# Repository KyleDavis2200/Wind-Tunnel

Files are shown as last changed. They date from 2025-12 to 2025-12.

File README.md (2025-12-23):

# Wind Tunnel
A DIY small scale wind tunnel made from everyday materials.


# Features
* Made from basic materials, allowing it to be remade by other people.
* Sturdy construction prevents collapse under high wind flow.
* Humidifier visualizes airflow to be seen through the viewing window.
* Includes jigs and drawings to aid in construction.

# Pictures







# Background

This wind tunnel uses a humidifier to create steam that will show the airflow over the model. The model is inserted into the tunnel, the window is screwed on, and then air flows through a funnel and a hose attached to the humidifier, into a straw inserted into the top of the model. The fan has a low, medium, and high speed setting allowing airflow to be visualized at different speeds. Most of the wind tunnel is built out of OSB, a cheap type of wood that is easily accessible. The collector part can be 3D printed, as that is the easiest way to make the smooth curve needed to guide the air into the tunnel. This wind tunnel is a little under 4 feet long and 9" square, and it can be built for under $100 if you already have a humidifier on hand.

# Bill of Materials

|Item |Price|Quantity |Total Price|Link |Notes: |
|---|-----|---|---|---|---|
|Fan |41.3 |1 |41.3 |https://www.amazon.com/dp/B0F11G5SWD?ref=ppx_yo2ov_dt_b_fed_asin_title&th=1 |*Sourcing from Amazon because a comparable fan on Aliexpress is usually more expensive, does not have adjustable speed, and may not have the right plug. We are also on a time crunch so I have already purchased this.|
|4'x8' 1/2" Sheet  of OSB |14.29|1 |14.29 |https://www.lowes.com/pd/1-2-CAT-PS2-10-OSB-Sheathing-Application-as-4-x-8/1000068915 | |
|1/4" ID, 3/8" OD Clear Tubing 10'|3.58 |1 |3.58 |https://www.lowes.com/pd/EZ-FLO-1-4-in-Inner-Diameter-x-10-ft-PVC-Clear-Vinyl-Tubing/1000365025 |*Sourcing from Lowe's because we have already bought this from there and are planning to get reimbursed |
|8"x10"x0.08" Acrylic |4.78 |1 |4.78 |https://www.lowes.com/pd/OPTIX-0-08-in-T-x-8-in-W-x-10-in-L-Clear-Acrylic-Sheet/3143395 |*Sourcing from Lowe's because we have already bought this from there and are planning to get reimbursed |
|#8 Wood Screws 1 5/8" Long |6.98 |1 (box of 75)|6.98 |https://www.lowes.com/pd/Hillman-8-x-1-5-8-in-Ceramic-Deck-Screws-75-Count/999995034 | |
|Caulk |2.98 |1 |2.98 |https://www.lowes.com/pd/DAP-Alex-Plus-10-1-oz-Clear-Paintable-Latex-Caulk/5004004945 |*Using to seal gaps that are letting air flow out through the corners of the tunnel. |
|Black Spray Paint |7.48 |1 |7.48 |https://www.lowes.com/pd/Krylon-FUSION-ALL-IN-ONE-Matte-Black-Spray-Paint-and-Primer-In-One-NET-WT-12-oz/1000460293|*Sourcing from Lowe's because we have already bought this from there and are planning to get reimbursed. Using to paint the inside of the tunnel black to provide contrast for the steam. |
|Humidifier |N/A  |1 |N/A |N/A |*Already have |
|Plastic Straw |N/A  |1 |N/A |N/A |*Already have |
|PLA Filament |N/A  |1kg |N/A |N/A |*Already have |
| | | | | | |
|Total Price: |N/A  |N/A |81.39 |N/A | |

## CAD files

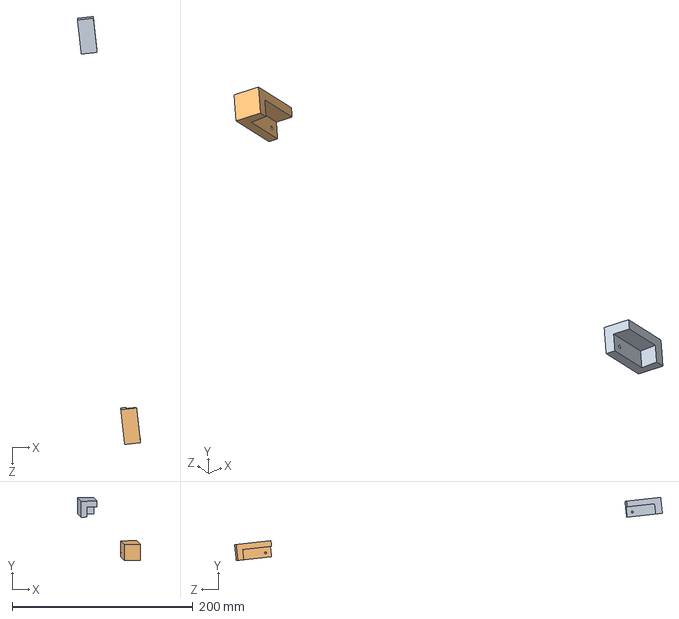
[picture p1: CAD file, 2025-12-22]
CAD/Jigs/Jigs HI.STEP
69.9 x 70.1 x 473.6 mm

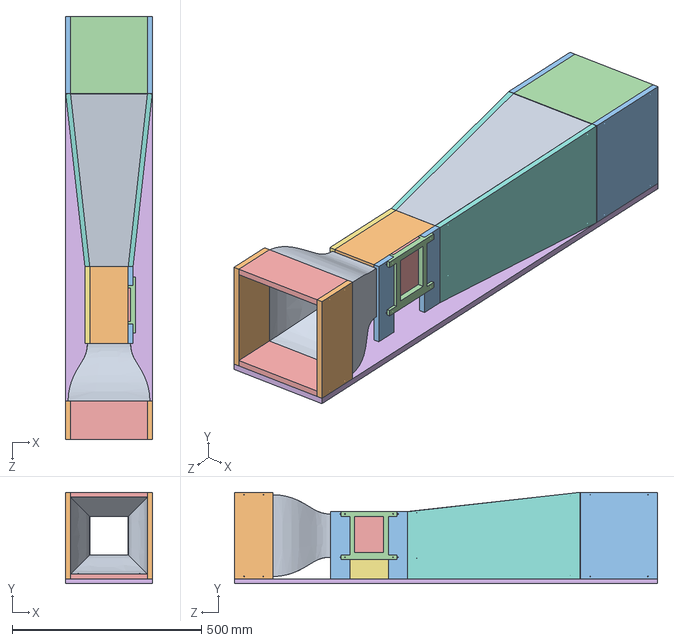
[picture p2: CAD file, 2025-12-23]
CAD/Wind Tunnel.STEP
228.6 x 241.4 x 1117.6 mm

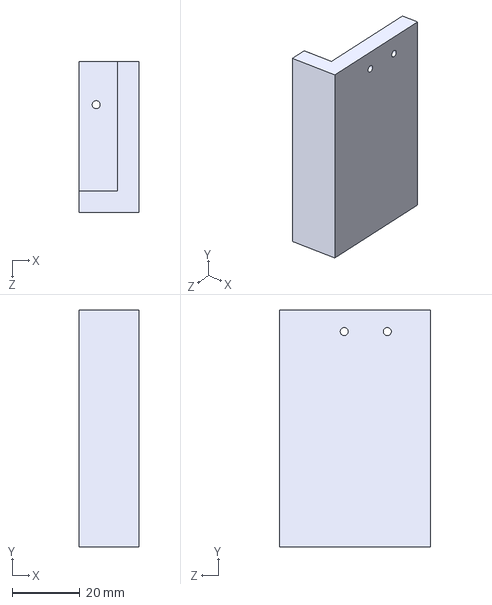
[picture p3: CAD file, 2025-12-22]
CAD/Jigs/Jig C.STEP
17.8 x 69.9 x 44.4 mm

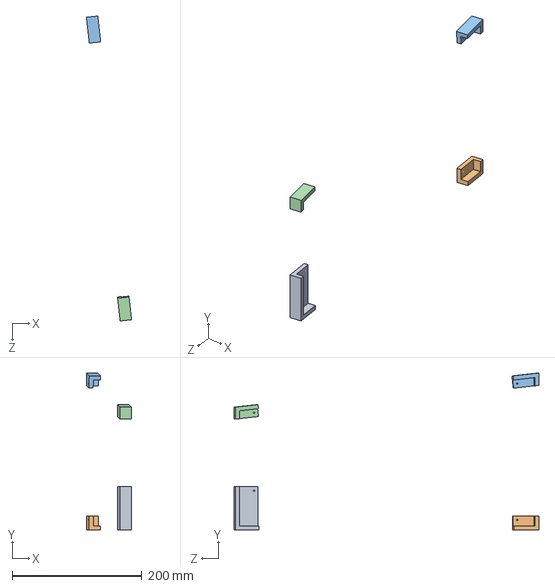
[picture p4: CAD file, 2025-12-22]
CAD/Jigs/Jigs DEFG.STEP
69.7 x 242.1 x 470.4 mm

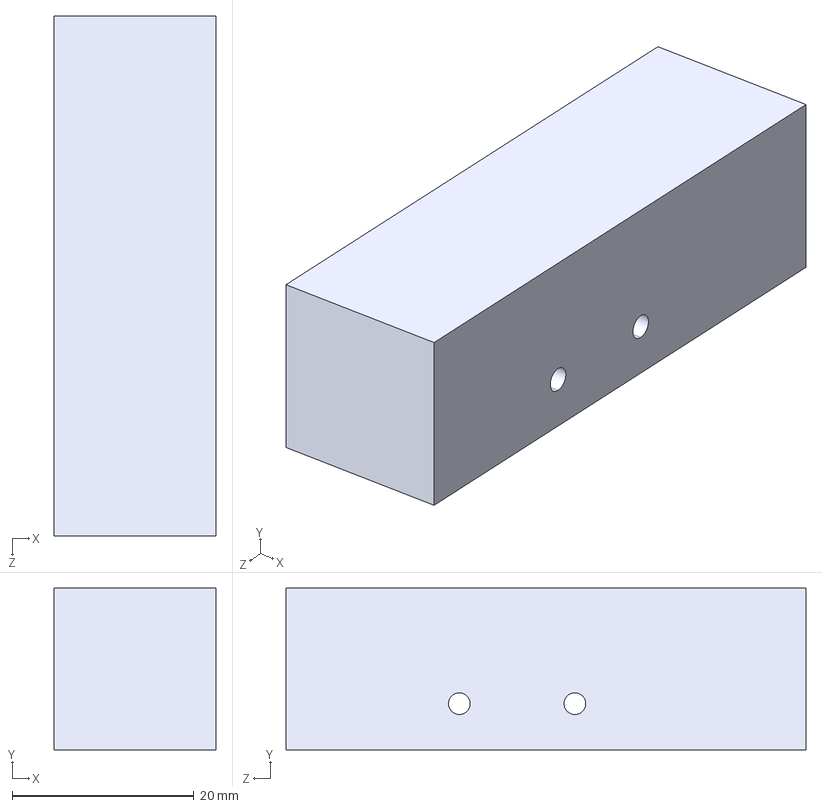
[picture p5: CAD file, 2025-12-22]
CAD/Jigs/Jig B.STEP
17.8 x 17.8 x 57.2 mm

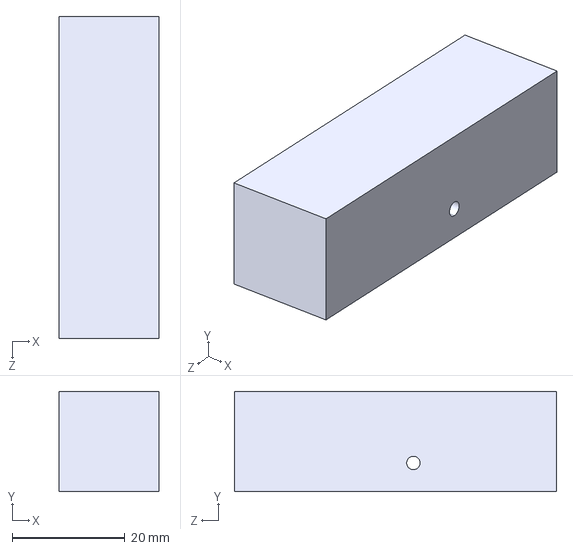
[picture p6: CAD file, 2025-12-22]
CAD/Jigs/Jig A.STEP
17.8 x 17.8 x 57.2 mm

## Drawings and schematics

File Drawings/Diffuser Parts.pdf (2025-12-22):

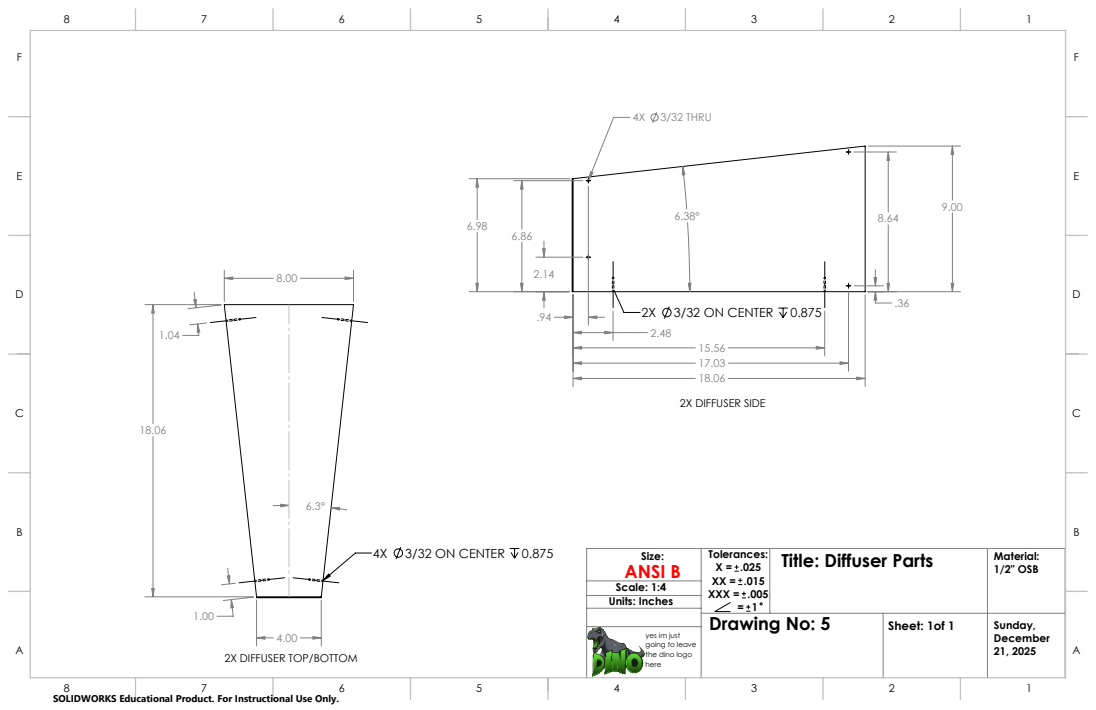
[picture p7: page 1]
Drawing No: 5; ANSI B; XXX =; Title: Diffuser Parts; Material:; 1/2" OSB; Scale: 1:4 Units: Inches; Sheet: 1of 1; 4X 3/32 THRU; 2X 3/32 ON CENTER 0.875; 4X 3/32 ON CENTER 0.875; 2X DIFFUSER SIDE; 2X DIFFUSER TOP/BOTTOM A

yes im just
going to leave
the dino logo
here

SOLIDWORKS Educational Product. For Instructional Use Only.

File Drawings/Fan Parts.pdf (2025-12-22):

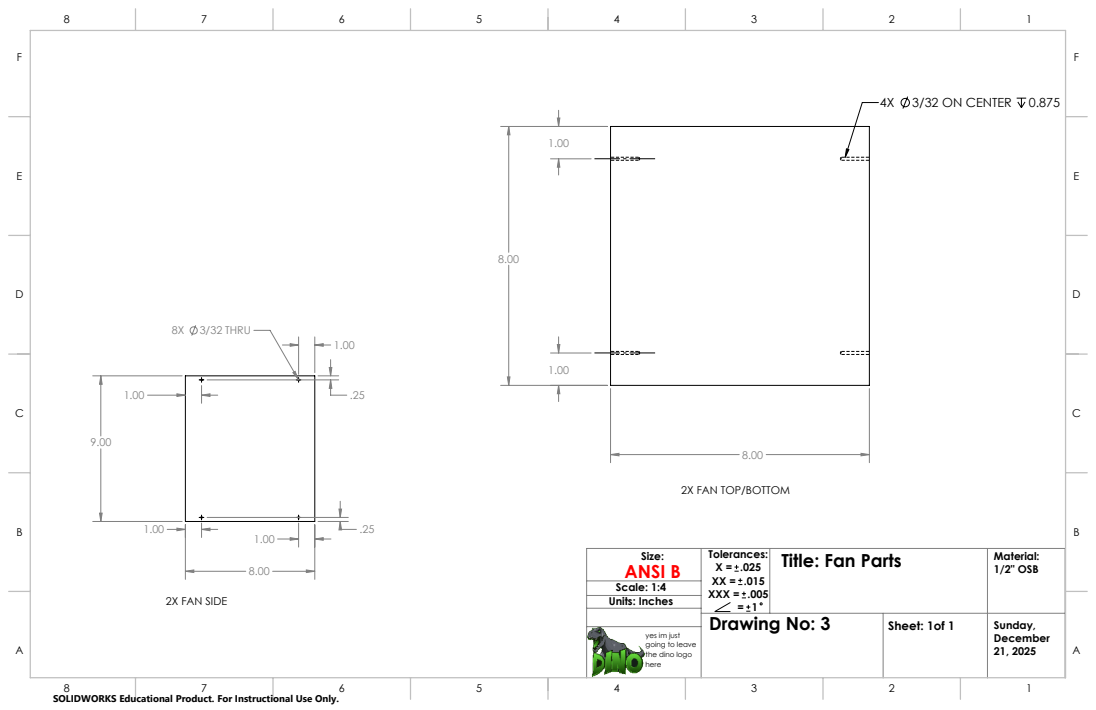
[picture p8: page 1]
Drawing No: 3; ANSI B; XXX =; Title: Fan Parts; Material:; 1/2" OSB; Scale: 1:4 Units: Inches; Sheet: 1of 1; 8X 3/32 THRU; 4X 3/32 ON CENTER 0.875; 2X FAN SIDE

2X FAN TOP/BOTTOM

yes im just
going to leave
the dino logo
here

SOLIDWORKS Educational Product. For Instructional Use Only.

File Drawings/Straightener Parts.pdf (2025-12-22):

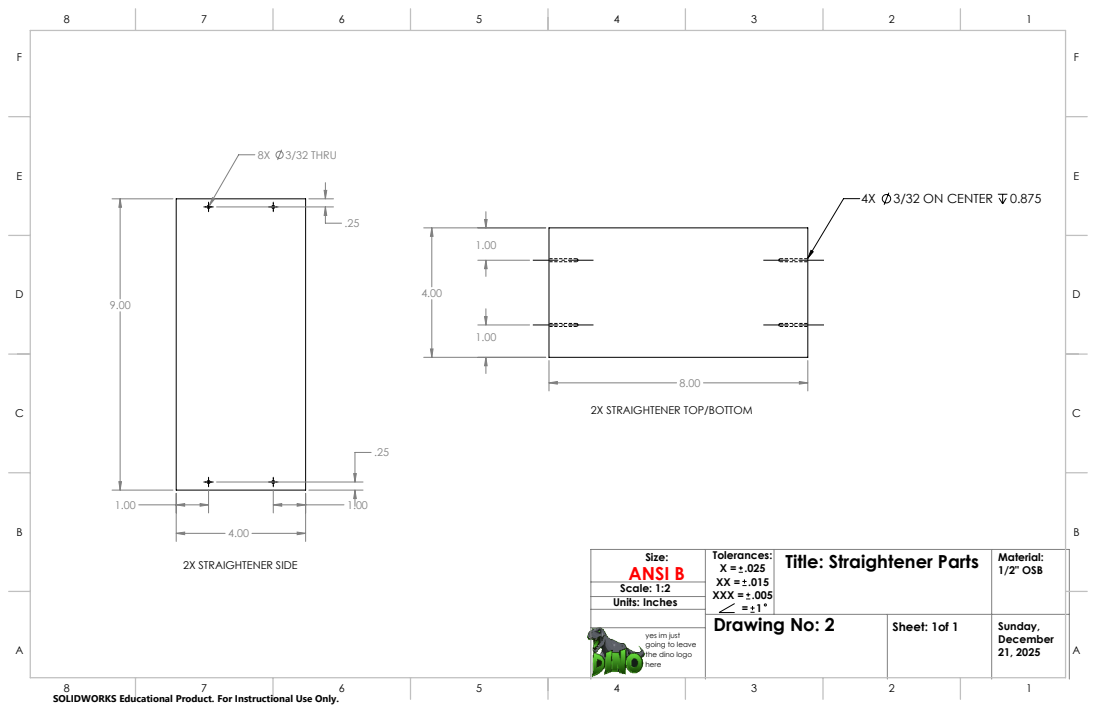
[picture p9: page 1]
Drawing No: 2; ANSI B; XXX =; Title: Straightener Parts; Material:; 1/2" OSB; Scale: 1:2 Units: Inches; Sheet: 1of 1; 8X 3/32 THRU; 4X 3/32 ON CENTER 0.875; 2X STRAIGHTENER SIDE

2X STRAIGHTENER TOP/BOTTOM

yes im just
going to leave
the dino logo
here

SOLIDWORKS Educational Product. For Instructional Use Only.

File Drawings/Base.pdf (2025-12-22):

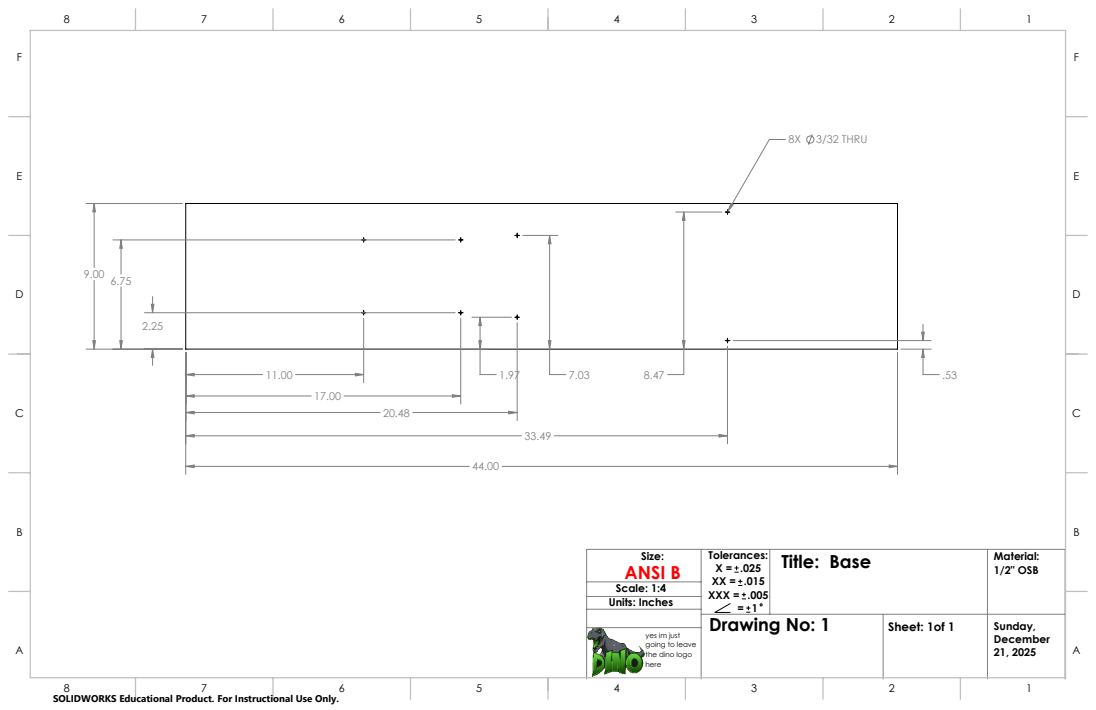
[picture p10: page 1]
Drawing No: 1; ANSI B; XXX =; Title: Base; Material:; 1/2" OSB; Scale: 1:4 Units: Inches; Sheet: 1of 1; 8X 3/32 THRU

yes im just
going to leave
the dino logo
here

SOLIDWORKS Educational Product. For Instructional Use Only.

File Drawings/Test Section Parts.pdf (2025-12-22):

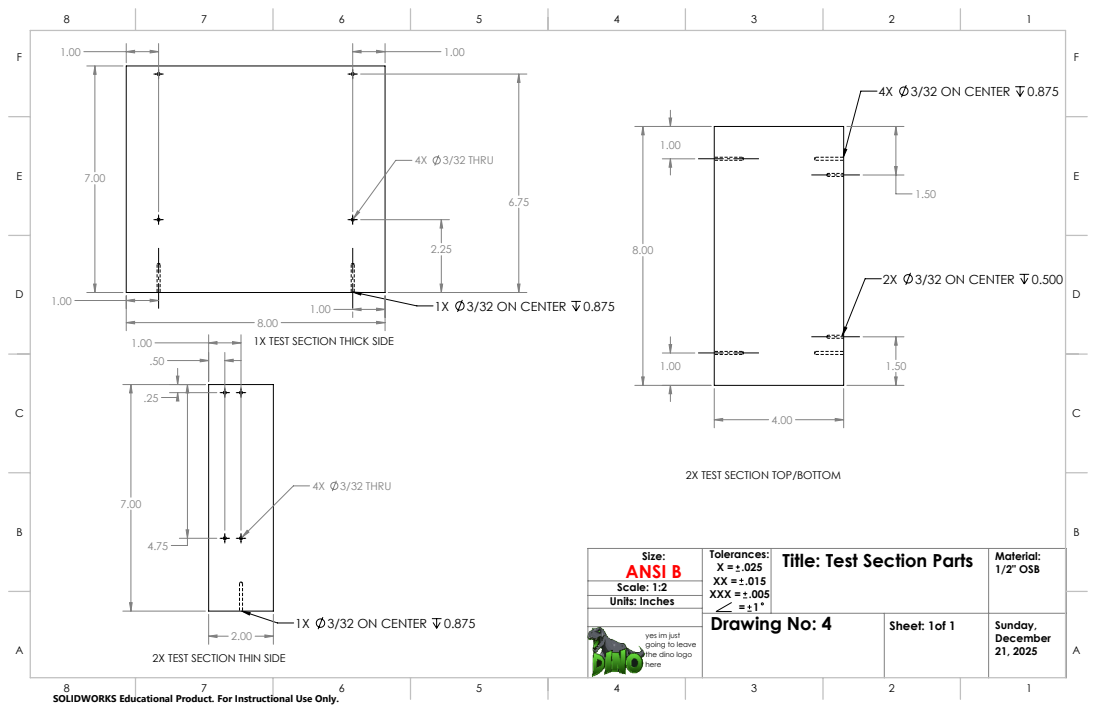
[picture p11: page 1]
Drawing No: 4; ANSI B; XXX =; Title: Test Section Parts; Material:; 1/2" OSB; Scale: 1:2 Units: Inches; Sheet: 1of 1; 4X 3/32 ON CENTER 0.875; 2X 3/32 ON CENTER 0.500; 4X 3/32 THRU; 1X 3/32 ON CENTER 0.875; 2X TEST SECTION THIN SIDE A

1X TEST SECTION THICK SIDE

2X TEST SECTION TOP/BOTTOM

yes im just
going to leave
the dino logo
here

SOLIDWORKS Educational Product. For Instructional Use Only.

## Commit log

2025-12-22 Rename Fan Parts.pdf to Drawings/Fan Parts.pdf
2025-12-22 Rename Drawings/Fan Parts.pdf to Drawings/Drawings/Fan Parts.pdf
2025-12-22 Rename Drawings/Drawings/Fan Parts.pdf to Drawings/Fan Parts.pdf
2025-12-22 Update and rename Jig A.STEP to CAD/Jigs/Jig A.STEP
    [Jig A.STEP]
2025-12-23 Revise README for clarity and additional details
    Updated the README to enhance clarity and provide additional details about the wind tunnel project, including features, pictures, and a bill of materials.
2025-12-23 Update and rename Wind Tunnel BOM - Sheet1.csv to BOM.csv
    [BOM.csv]
